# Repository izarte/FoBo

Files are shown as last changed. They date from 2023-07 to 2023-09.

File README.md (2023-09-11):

# Fobo
This project is the final degree work in robotic engineering.
Fobo is a robot whose main task is to follow you to carry your heavy weights.

It is based on a webcam with 2 degrees of freedom thanks to 2 servomotors, which, using [YOLOv8] can detect and track people in its image. The camera will follow the objective person and the robot will move based on the servomotor's position. The robot also has a depth camera used to avoid obstacles.

# Demo
Real demostration video (click on image of real FoBo):

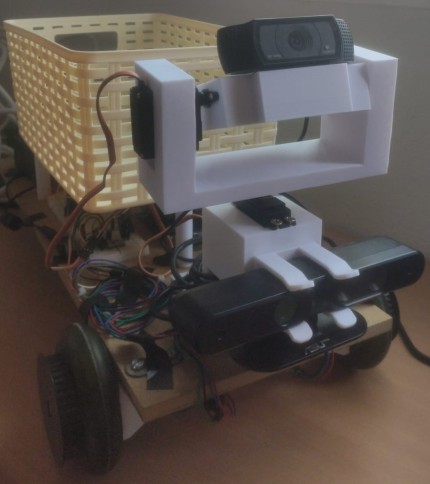
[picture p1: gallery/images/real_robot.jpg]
Demo (https://www.youtube.com/watch?v=qhu7xcjDXUQ)


# Model
All Fobo chassis have been modeled to be printed in a 3d printer. The total model can be found in [full-model]. To make the printing process easier divided model can be found in [divided-full-model].

Essential pieces to attach to a wooden board can be found in [final-real-pieces]

# Hardware
To create this robot it is necessary:
 1. NVIDIA Jetson Nano 2GB (5V 3A current)
 2. Arduino Uno
 3. Asus Xtion Pro Live
 4. Logitech C920 HD Pro Webcam
 5. 2x Stepper Motor NEMA17 (12V 2A current)
 6. 2x A4988 Stepper Driver
 7. 2x 1N4004 Diode
 8. 2x Servomotor mg945
 9. IMU MPU-6050

The following diagram shows how devices are connected

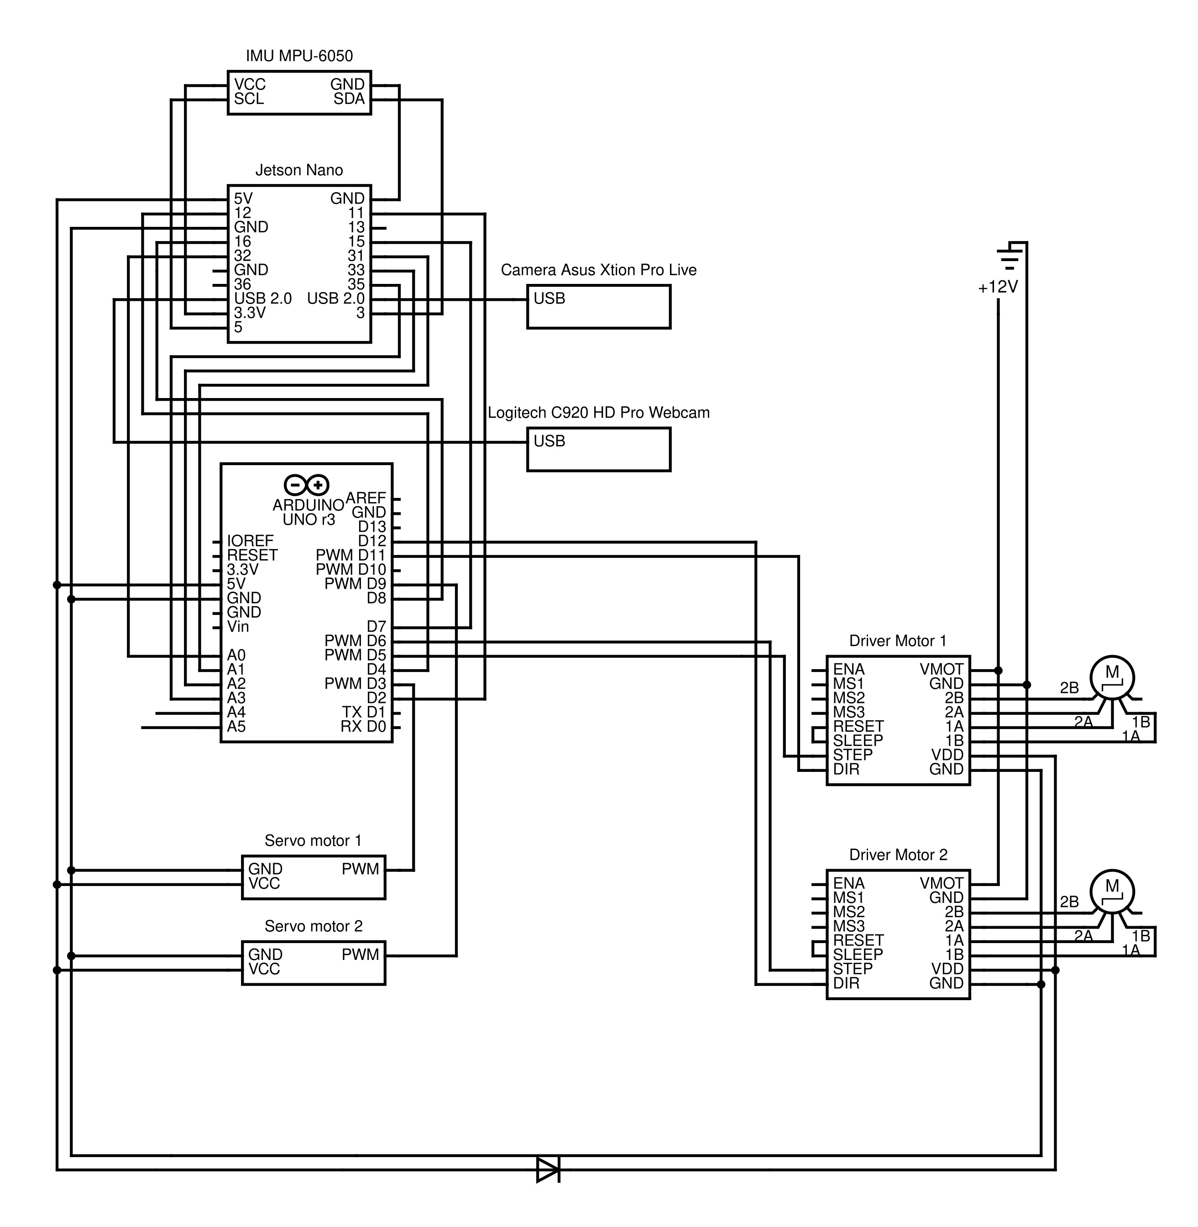
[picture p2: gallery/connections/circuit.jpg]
circuit


# Software
## Arduino

Arduino code can be found in [arduino]. This folder is a Platformio project. Code can be uploaded to Arduino via platformio.

## Jetson

### Prerequisites
1. Jetpack 4.6.2 (version L4T 32.7.1)
2. Docker (with docker-compose)

Go to [openni], a modified repository to execute in jetson nano based on [OpenNI2], and follow repository instructions.
Go to [ros2-ws] and execute the following commands to create a symbolic link to the dynamic library.
```
ln -s /usr/lib/OpenNI2
ln -s /usr/lib/libOpenNI2.so
```

After OpeNI installation, go to [jetson] folder and execute:
```
docker compose up
```

[YOLOv8]: https://github.com/ultralytics/ultralytics
[full-model]: https://github.com/izarte/FoBo/tree/main/model/full_model
[divided-full-model]: https://github.com/izarte/FoBo/tree/main/model/divided_full_model
[final-real-pieces]: https://github.com/izarte/FoBo/tree/main/model/final_real_pieces
[circuit]: https://github.com/izarte/FoBo/blob/main/gallery/connections/circuit.jpg
[arduino]: https://github.com/izarte/FoBo/tree/main/arduino
[openni]: https://github.com/izarte/FoBo/tree/main/jetson/openni/OpenNI2-TX1/OpenNI2
[OpenNI2]: https://github.com/mikeh9/OpenNI2-TX1/tree/master/OpenNI2
[ros2-ws]: https://github.com/izarte/FoBo/tree/main/jetson/ros2_ws
[jetson]: https://github.com/izarte/FoBo/tree/main/jetson

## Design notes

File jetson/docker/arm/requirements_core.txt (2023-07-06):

Jetson.GPIO==2.0.20
numpy==1.24.2
opencv-python==4.7.0.72
smbus==1.1.post2
simple-pid==2.0.0
websockets==9.1

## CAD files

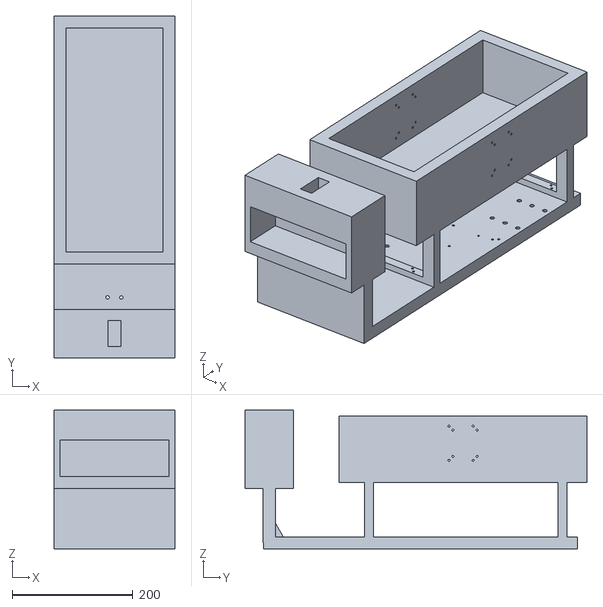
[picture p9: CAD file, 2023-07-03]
jetson/ros2_ws/src/fobo_simulation/models/own/meshes/total_model.stl
200.0 x 565.6 x 230.0

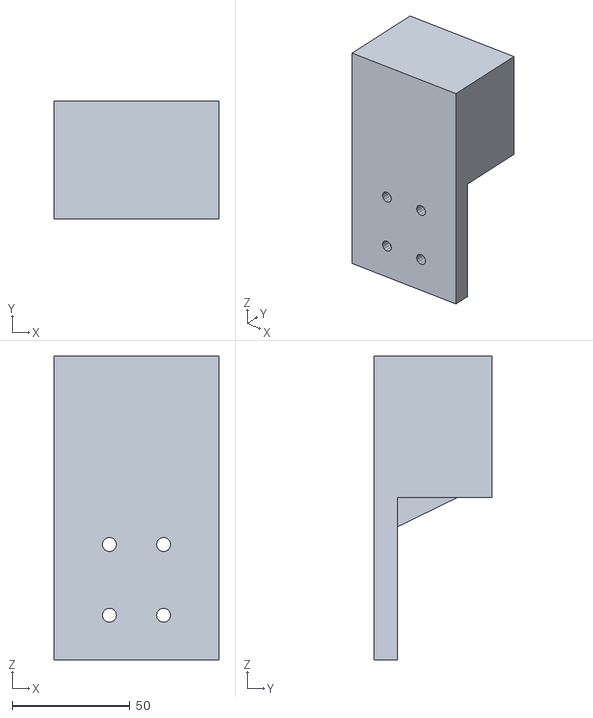
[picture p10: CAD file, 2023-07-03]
model/divided_full_model/stl/servo_piece.stl
70.0 x 50.0 x 129.0

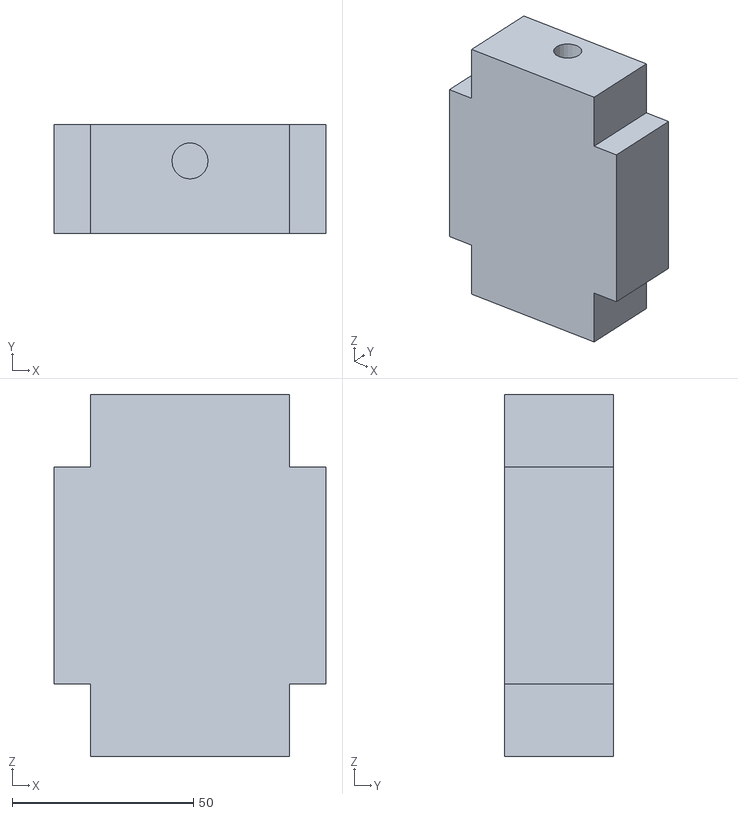
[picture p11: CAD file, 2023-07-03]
model/final_real_pieces/stl/camera_support.stl
75.0 x 30.0 x 100.0

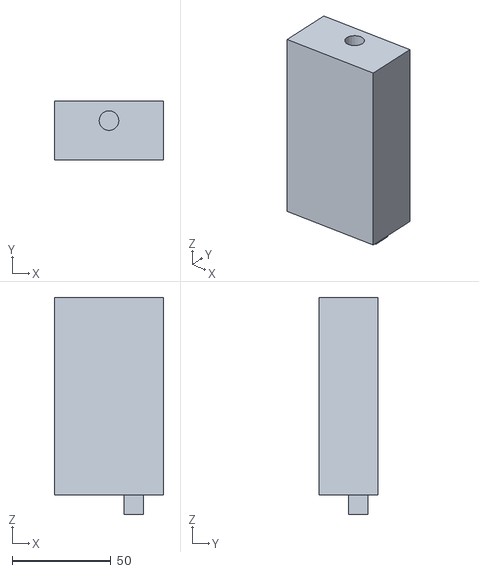
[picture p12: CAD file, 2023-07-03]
model/full_model/camera_support_2.stl
55.0 x 30.0 x 110.0

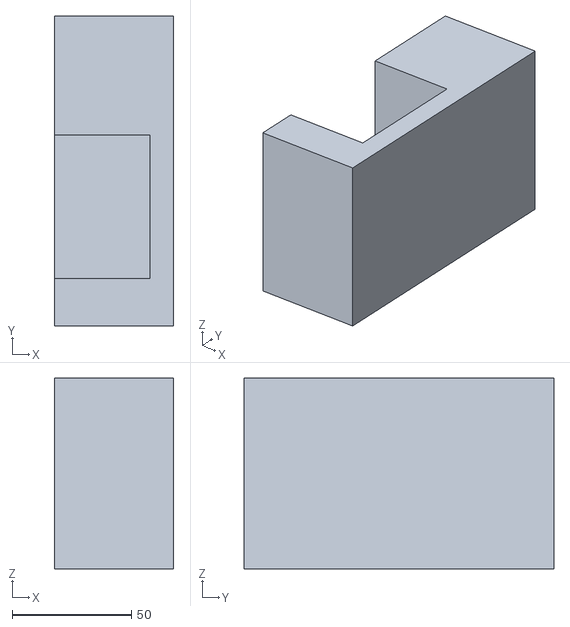
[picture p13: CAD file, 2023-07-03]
model/divided_full_model/stl/front_support_4.stl
50.0 x 130.0 x 80.0

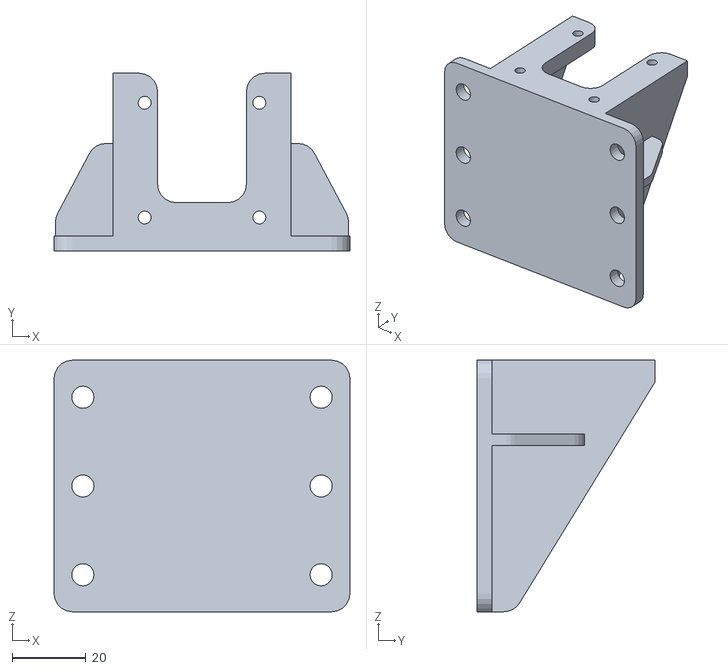
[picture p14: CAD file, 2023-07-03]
model/final_real_pieces/stl/nema17bracket_v2.stl
80.0 x 48.0 x 68.0

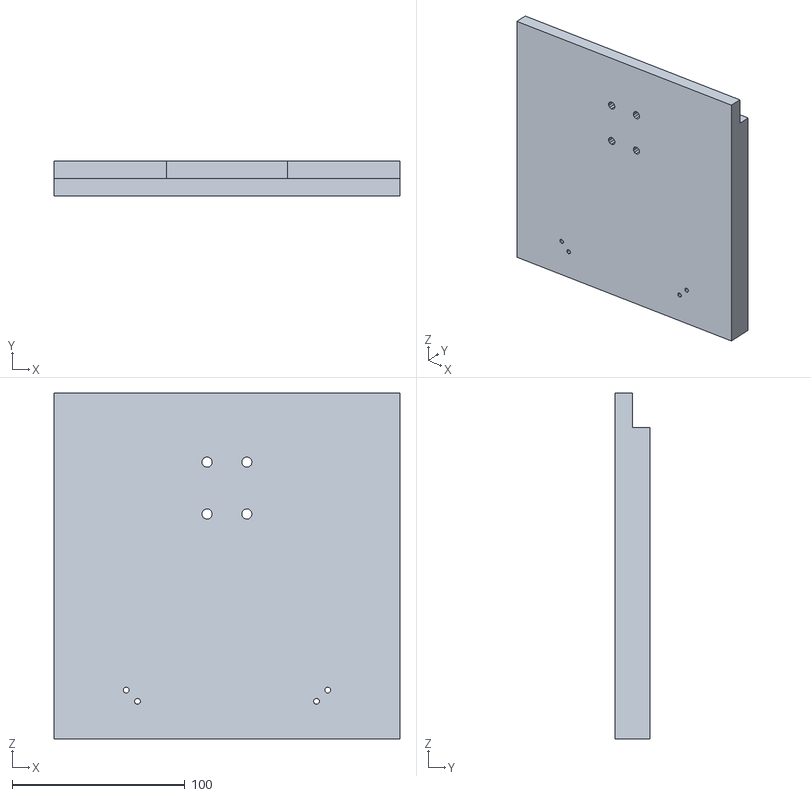
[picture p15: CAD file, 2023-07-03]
model/full_model/base_front.stl
200.0 x 20.0 x 200.0

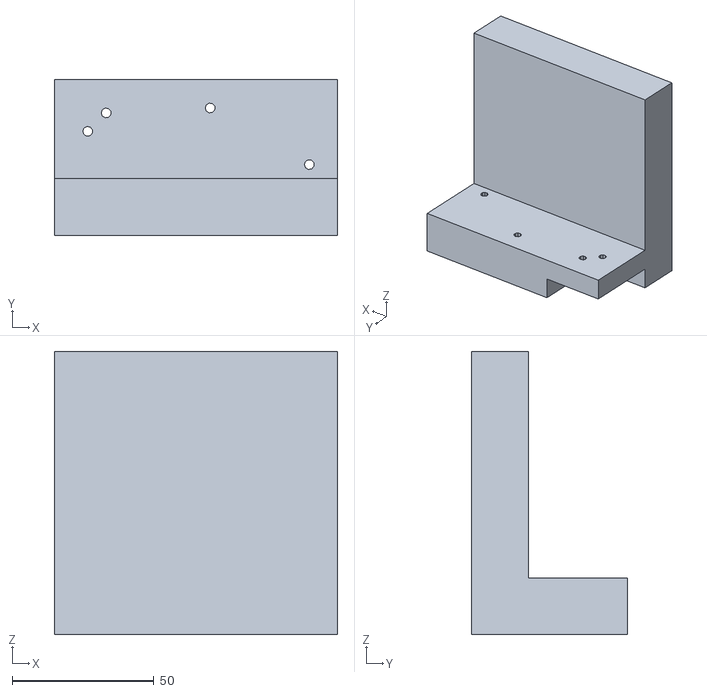
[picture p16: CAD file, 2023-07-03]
model/divided_full_model/stl/container_back_head_3.stl
100.0 x 55.0 x 100.0

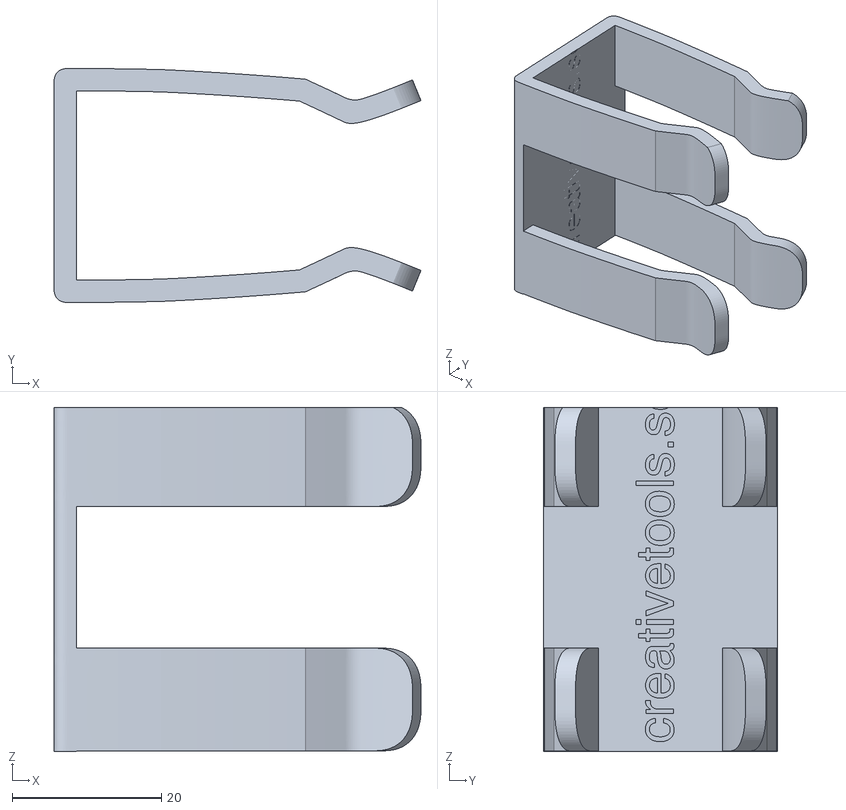
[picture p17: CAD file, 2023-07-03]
model/final_real_pieces/stl/clip_depth_camera.stl
49.3 x 31.4 x 46.2

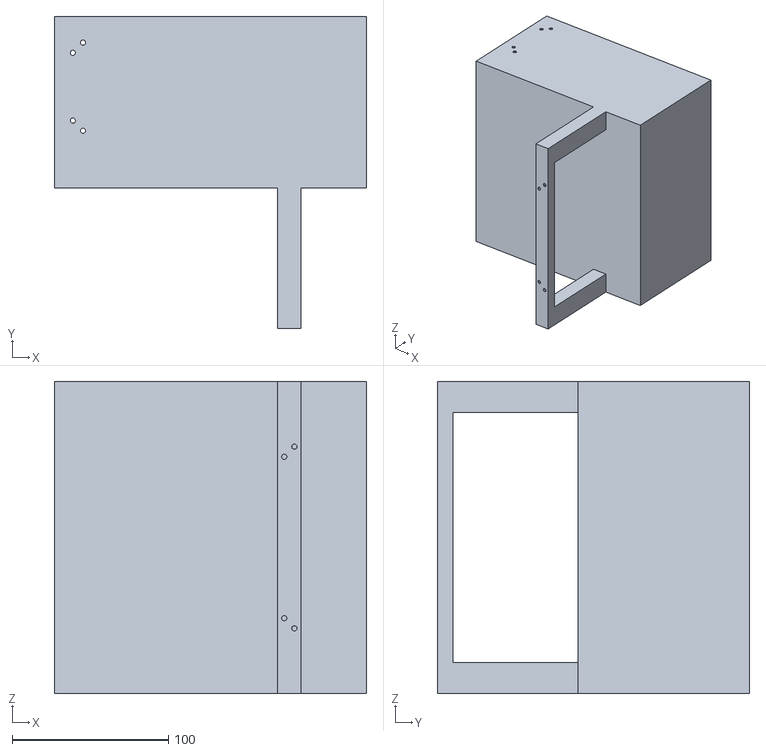
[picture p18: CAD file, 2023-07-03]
model/full_model/container_front.stl
200.0 x 200.0 x 200.0

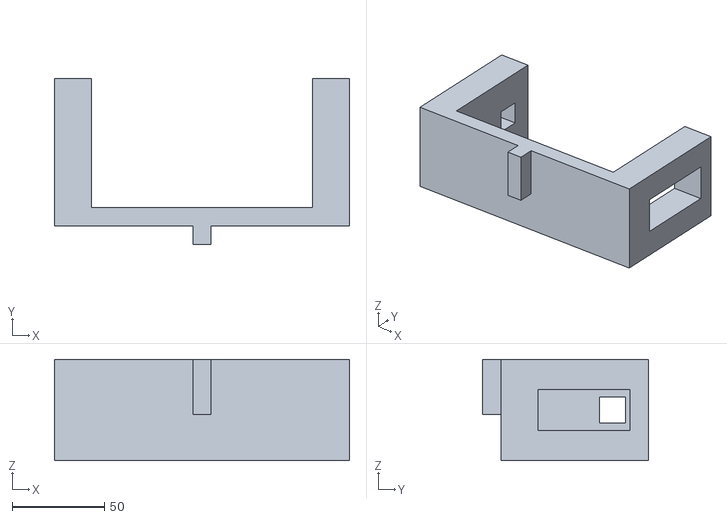
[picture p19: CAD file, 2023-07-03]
model/final_real_pieces/stl/camera_support_support.stl
160.0 x 90.0 x 55.0

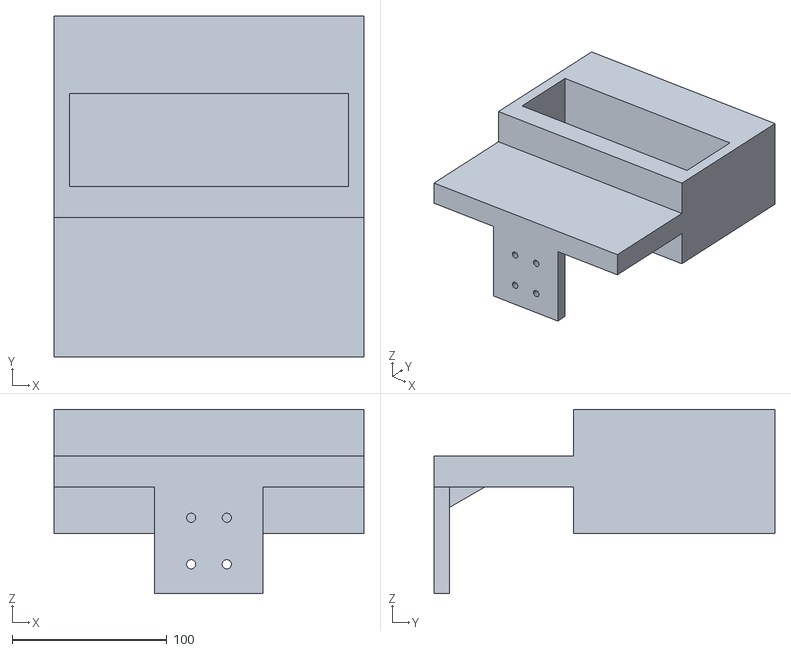
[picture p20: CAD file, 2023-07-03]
model/full_model/front_support.stl
200.0 x 220.0 x 119.0

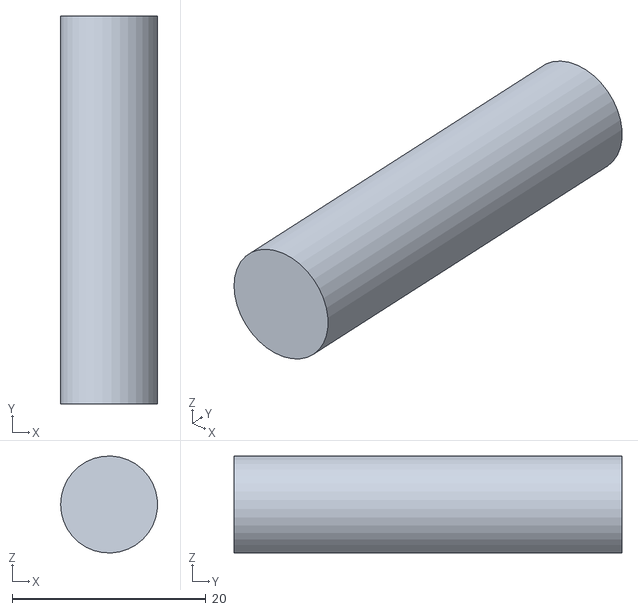
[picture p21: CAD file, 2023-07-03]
model/final_real_pieces/stl/union.stl
9.98 x 40.0 x 9.99

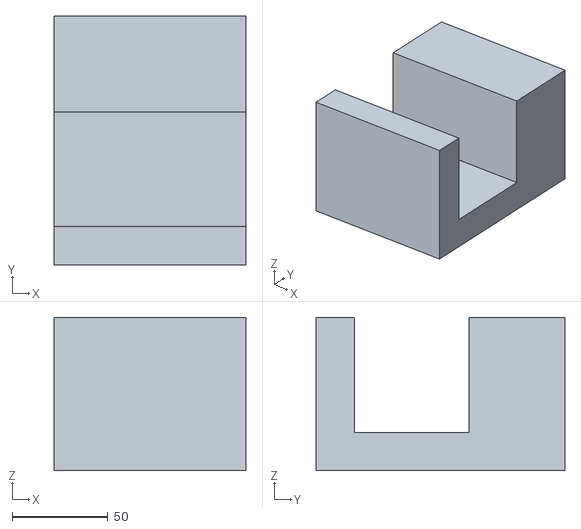
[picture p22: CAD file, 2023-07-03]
model/divided_full_model/stl/front_support_3.stl
100.0 x 130.0 x 80.0

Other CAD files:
jetson/ros2_ws/src/fobo_simulation/models/tuto/meshes/total_model.stl
model/divided_full_model/stl/front_support_2.stl
model/full_model/camera_support.stl
model/divided_full_model/4_center_union.ipt
model/divided_full_model/OldVersions/base_back.0004.ipt
model/divided_full_model/OldVersions/base_front.0004.ipt
model/divided_full_model/OldVersions/base_mid.0005.ipt
model/divided_full_model/OldVersions/camera_support.0002.ipt
model/divided_full_model/OldVersions/camera_support_2.0003.ipt
model/divided_full_model/OldVersions/container_back_foot_1.0001.ipt
model/divided_full_model/OldVersions/container_back_foot_1.0001_1.ipt
model/divided_full_model/OldVersions/container_back_head.0001.ipt
model/divided_full_model/OldVersions/container_back_head_5.0001.ipt
model/divided_full_model/OldVersions/container_back_head_7.0001.ipt
model/divided_full_model/OldVersions/container_front_foot_1.0001.ipt
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

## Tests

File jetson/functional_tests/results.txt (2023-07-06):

0:
    112
    120
    133
    123
    118
0.51:
    101
    120
    118
    126
    112
1.2:
    98
    101
    113
    115
    101

1.7:
    80
    98
    108
    110
    80
    106

2.98:
    62
    68
    56
    30
    65

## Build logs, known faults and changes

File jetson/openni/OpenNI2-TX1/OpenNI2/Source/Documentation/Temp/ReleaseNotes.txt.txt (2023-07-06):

/** @page release_notes Release Notes
OpenNI 2.3.0 Build 15
November 10 2013

Minimum Requirements:
---------------------
- Operating Systems: 
  - Windows XP with SP2 and above, Windows 7, Windows 8, on x86 (32/64 bit)
  - Ubuntu 12.04 (32/64/arm) and above
  - Android 2.3 and above
  - Mac OSX 10.7 and above
- Processors: 
  - Pentium 4, 1.4GHz and above 
  - AMD Athlon 64/FX 1GHz and above
  - Arm Cortex A8 and above
- Memory: at least 64MB available.
- 250MB free hard disk space.
- Available USB 2.0 high-speed port.
- Development Environment: 
  - Microsoft Visual Studio 2008 and 2010. The compiler can be MSVC compiler or an Intel Compiler 11 and above.
  - GCC 4.x
- Some of the sample applications require a graphics card equivalent to: ATI RADEON x1300 or NVIDIA GeForce 7300.

Prerequisets:
-------------
- Windows:
  - Microsoft Kinect SDK v1.6 (for using with Kinect devices)
    From: http://go.microsoft.com/fwlink/?LinkID=262831

- Linux:
  - LibUSB 1.0.x
    From: http://sourceforge.net/projects/libusb/files/libusb-1.0/
    Or via apt:
    sudo apt-get install libusb-1.0-0
  - LibUDEV
    sudo apt-get install libudev0
  - FreeGLUT3
    From: http://freeglut.sourceforge.net/index.php#download
    You only need the run-time version to run the OpenGL samples:
    sudo apt-get install freeglut3
    If you also want to compile the OpenGL samples, you'll need to install the development version:
    sudo apt-get install freeglut3-dev

Notes:
------
- On Android, only native support (and samples) is currently provided. Please note that as bionic (Android linker) does not
  support the rpath option, the samples cannot start as is. To solve this, do one of the following:
  - Copy OpenNI libraries (libOpenNI2.so, libPS1080.so and libOniFile.so) to /system/lib (requires root) - or -
  - run `export LD_LIBRARY_PATH=.:$LD_LIBRARY_PATH` before starting the native executeable

*/

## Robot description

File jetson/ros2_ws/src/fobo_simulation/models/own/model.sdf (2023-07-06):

<?xml version="1.0" ?>
<sdf version="1.7">
  <model name="fobo" xmlns:xacro="http://ros.org/wiki/xacro">
    <pose>0.0 0.0 0.0 0.0 0.0 0.0</pose>

    <link name="base_footprint"/>

    <joint name="base_joint" type="fixed">
      <parent>base_footprint</parent>
      <child>base_link</child>
      <pose>0.0 0.0 0.000 0 0 0</pose>
    </joint>

    <link name="base_link">
      <visual name="base_visual">
        <pose>0 0 0 0 0 0</pose>
        <geometry>
          <mesh>
            <uri>model://own/meshes/total_model.stl</uri>
            <scale>0.001 0.001 0.001</scale>
          </mesh>
        </geometry>
      </visual>



      <collision name="base_collision">
        <pose>0.1175 0.5 0.5 0 0 0</pose>
        <geometry>
          <box>
            <size>0. 0. 0.</size>
          </box>
        </geometry>
      </collision>
    </link>


    <joint name="wheel_left_joint" type="revolute">
      <parent>base_link</parent>
      <child>wheel_left_link</child>
      <pose>0.235 0.4 0.05 0 1.57 0</pose>
      <axis>
        <xyz>0 0 1</xyz>
      </axis>
    </joint>

    <link name="wheel_left_link">
      <collision name="wheel_left_collision">
        <pose>0.235 0.4 0.05 0 1.57 0</pose>
        <geometry>
          <cylinder>
            <radius>0.033</radius>
            <length>0.018</length>
          </cylinder>
        </geometry>
        <surface>
          <!-- This friction pamareter don't contain reliable data!! -->
          <friction>
            <ode>
              <mu>100000.0</mu>
              <mu2>100000.0</mu2>
              <fdir1>0 0 0</fdir1>
              <slip1>0.0</slip1>
              <slip2>0.0</slip2>
            </ode>
          </friction>
          <contact>
            <ode>
              <soft_cfm>0</soft_cfm>
              <soft_erp>0.2</soft_erp>
              <kp>1e+5</kp>
              <kd>1</kd>
              <max_vel>0.01</max_vel>
              <min_depth>0.001</min_depth>
            </ode>
          </contact>
        </surface>
      </collision>

      <visual name="wheel_left_visual">
        <pose>0.235 0.4 0.05 0 1.57 0</pose>
        <geometry>
          <cylinder>
            <radius>0.033</radius>
            <length>0.018</length>
          </cylinder>
        </geometry>
      </visual>
    </link>


    <joint name="wheel_right_joint" type="revolute">
      <parent>base_link</parent>
      <child>wheel_right_link</child>
      <pose>0.01 0.4 0.05 0 1.57 0</pose>
      <axis>
        <xyz>0 0 1</xyz>
      </axis>
    </joint>

    <link name="wheel_right_link">
      <collision name="wheel_right_collision">
        <pose>0.01 0.4 0.05 0 1.57 0</pose>
        <geometry>
          <cylinder>
            <radius>0.033</radius>
            <length>0.018</length>
          </cylinder>
        </geometry>
        <surface>
          <!-- This friction pamareter don't contain reliable data!! -->
          <friction>
            <ode>
              <mu>100000.0</mu>
              <mu2>100000.0</mu2>
              <fdir1>0 0 0</fdir1>
              <slip1>0.0</slip1>
              <slip2>0.0</slip2>
            </ode>
          </friction>
          <contact>
            <ode>
              <soft_cfm>0</soft_cfm>
              <soft_erp>0.2</soft_erp>
              <kp>1e+5</kp>
              <kd>1</kd>
              <max_vel>0.01</max_vel>
              <min_depth>0.001</min_depth>
            </ode>
          </contact>
        </surface>
      </collision>

      <visual name="wheel_right_visual">
        <pose>0.01 0.4 0.05 0 1.57 0</pose>
        <geometry>
          <cylinder>
            <radius>0.033</radius>
            <length>0.018</length>
          </cylinder>
        </geometry>
      </visual>
    </link>


    <joint name="wheel_front_joint" type="revolute">
      <parent>base_link</parent>
      <child>wheel_front_link</child>
      <pose>0.1157 0.08 0.05 0 1.57 0</pose>
      <axis>
        <xyz>0 0 1</xyz>
      </axis>
    </joint>

    <link name="wheel_front_link">
      <collision name="wheel_front_collision">
        <pose>0.1157 0.08 0.05 0 1.57 0</pose>
        <geometry>
          <cylinder>
            <radius>0.033</radius>
            <length>0.018</length>
          </cylinder>
        </geometry>
        <surface>
          <!-- This friction pamareter don't contain reliable data!! -->
          <friction>
            <ode>
              <mu>100000.0</mu>
              <mu2>100000.0</mu2>
              <fdir1>0 0 0</fdir1>
              <slip1>0.0</slip1>
              <slip2>0.0</slip2>
            </ode>
          </friction>
          <contact>
            <ode>
              <soft_cfm>0</soft_cfm>
              <soft_erp>0.2</soft_erp>
              <kp>1e+5</kp>
              <kd>1</kd>
              <max_vel>0.01</max_vel>
              <min_depth>0.001</min_depth>
            </ode>
          </contact>
        </surface>
      </collision>

      <visual name="wheel_front_visual">
        <pose>0.1157 0.08 0.05 0 1.57 0</pose>
        <geometry>
          <cylinder>
            <radius>0.033</radius>
            <length>0.018</length>
          </cylinder>
        </geometry>
      </visual>
    </link>

  </model>
</sdf>

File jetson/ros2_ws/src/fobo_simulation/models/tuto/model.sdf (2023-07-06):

<?xml version='1.0'?>
<sdf version='1.7'>
  <model name="tuto">
    <static>false</static>

    <link name="base_footprint"/>

    <joint name="base_joint" type="fixed">
      <parent>base_footprint</parent>
      <child>base_link</child>
      <pose>0.0 0.0 0.010 0 0 0</pose>
    </joint>

    <link name='base_link'>
      <pose>0 0 .1 0 0 0</pose>
    
      <collision name='collision'>
        <geometry>
          <box>
            <size>.4 .2 .1</size>
          </box>
          <pose>-0.15 0 .1 0 0 0</pose>
          <box>
            <size>0.1 .2 .1</size>
          </box>
        </geometry>
      </collision>
    
      <visual name='visual'>
        <geometry>
          <box>
            <size>.4 .2 .1</size>
          </box>
        </geometry>
      </visual>

      <visual name='front_up'>
      <pose>-0.15 0 .1 0 0 0</pose>
        <geometry>
          <box>
            <size>0.1 .2 .1</size>
          </box>
        </geometry>
      </visual>

      <collision name='caster_collision'>
        <pose>-0.15 0 -0.05 0 0 0</pose>
        <geometry>
            <sphere>
            <radius>.05</radius>
          </sphere>
        </geometry>
      
        <surface>
          <friction>
            <ode>
              <mu>0</mu>
              <mu2>0</mu2>
              <slip1>1.0</slip1>
              <slip2>1.0</slip2>
            </ode>
          </friction>
        </surface>
      </collision>
      
      <visual name='caster_visual'>
        <pose>-0.15 0 -0.05 0 0 0</pose>
        <geometry>
          <sphere>
            <radius>.05</radius>
          </sphere>
        </geometry>
      </visual>
    </link>


    <link name="wheel_left_link">
      <pose>0.1 0.13 0.1 0 1.5707 1.5707</pose>
      <collision name="collision">
        <geometry>
          <cylinder>
            <radius>.1</radius>
            <length>.05</length>
          </cylinder>
        </geometry>
      </collision>
      <visual name="visual">
        <geometry>
          <cylinder>
            <radius>.1</radius>
            <length>.05</length>
          </cylinder>
        </geometry>
      </visual>
    </link>

    <link name="wheel_right_link">
      <pose>0.1 -0.13 0.1 0 1.5707 1.5707</pose>
      <collision name="collision">
        <geometry>
          <cylinder>
            <radius>.1</radius>
            <length>.05</length>
          </cylinder>
        </geometry>
      </collision>
      <visual name="visual">
        <geometry>
          <cylinder>
            <radius>.1</radius>
            <length>.05</length>
          </cylinder>
        </geometry>
      </visual>
    </link>

    <joint type="revolute" name="wheel_left_joint">
      <pose>0 0 -0.03 0 0 0</pose>
      <parent>base_link</parent>
      <child>wheel_left_link</child>
      <axis>
        <xyz>0 0 -1</xyz>
      </axis>
    </joint>
    
    <joint type="revolute" name="wheel_right_joint">
      <pose>0 0 0.03 0 0 0</pose>
      <parent>base_link</parent>
      <child>wheel_right_link</child>
      <axis>
        <xyz>0 0 -1</xyz>
      </axis>
    </joint>


    <link name="camera_link">
      <pose>-0.15 0 .3 0 0 0</pose>
      <collision name="collision">
        <geometry>
          <box>
            <size>0.05 .1 .05</size>
          </box>
        </geometry>
      </collision>
      <visual name="visual">
        <geometry>
          <box>
            <size>0.05 .1 .05</size>
          </box>
        </geometry>
      </visual>

      <sensor name="depth_camera" type="camera">
        <always_on>true</always_on>
        <visualize>false</visualize>
        <update_rate>5</update_rate>
        <camera name="camera">
          <horizontal_fov>1.02974</horizontal_fov>
          <image>
            <width>640</width>
            <height>480</height>
            <format>R8G8B8</format>
          </image>
          <clip>
            <near>0.02</near>
            <far>10</far>
          </clip>
          <noise>
            <type>gaussian</type>
            <!-- Noise is sampled independently per pixel on each frame.
                That pixel's noise value is added to each of its color
                  channels, which at that point lie in the range [0,1]. -->
            <mean>0.0</mean>
            <stddev>0.007</stddev>
          </noise>
        </camera>
        <plugin name="depth_camera_controller" filename="libgazebo_ros_camera.so">
          <camera_name>camera_link</camera_name>
          <frame_name>camera_link_frame</frame_name>
          <hack_baseline>0</hack_baseline>
          <min_depth>0.001</min_depth>
        </plugin>
      </sensor>
    </link>

    <joint type="revolute" name="camera_base_joint">
      <pose>-0.15 0 .3 0 0 0</pose>
      <parent>base_link</parent>
      <child>camera_link</child>
      <axis>
        <xyz>1 0 0</xyz>
      </axis>
    </joint>

    <transmission name="camera_base_tran">
      <type>transmission_interface/SimpleTransmission</type>
      <joint name="camera_base_joint">
        <hardwareInterface>EffortJointInterface</hardwareInterface>
      </joint>
      <actuator name="camera_base">
        <mechanicalReduction>1.0</mechanicalReduction>
        <hardwareInterface>EffortJointInterface</hardwareInterface>
      </actuator>
    </transmission>

    <gazebo>
      <plugin name="gazebo_ros_control" filename="libgazebo_ros_control.so">
        <robotNamespace>/fobo</robotNamespace>
      </plugin>
    </gazebo>

    <!-- Controls the differential drive robot -->
    <plugin name='diff_drive' filename='libgazebo_ros_diff_drive.so'>
      <ros>
        <namespace>/fobo</namespace>
        <remapping>cmd_vel:=cmd_vel</remapping>
        <remapping>odom:=odom</remapping>
      </ros>

      <!-- wheels -->
      <left_joint>wheel_left_joint</left_joint>
      <right_joint>wheel_right_joint</right_joint>

      <!-- kinematics -->
      <wheel_separation>0.26</wheel_separation>
      <wheel_diameter>0.2</wheel_diameter>

      <!-- limits -->
      <max_wheel_torque>20</max_wheel_torque>
      <max_wheel_acceleration>1.0</max_wheel_acceleration>

      <!-- output -->
      <publish_odom>true</publish_odom>
      <publish_odom_tf>true</publish_odom_tf>
      <publish_wheel_tf>true</publish_wheel_tf>

      <odometry_frame>odom</odometry_frame>
      <robot_base_frame>chassis</robot_base_frame>
    </plugin>
  </model>
</sdf>

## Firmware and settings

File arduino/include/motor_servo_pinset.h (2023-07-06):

#ifndef MOTOR_SERVO_PINSET_H

#define MOTOR_SERVO_PINSET_H

#include <Servo.h>
#include <Arduino.h>

// init.cpp
void init_servos();
void init_motors();

// servo.cpp
void servo_control();
void modify_angle(int *angle, int delta);
void blinkLed(int t);

// Stepper
void motors_control();

const int LED = 13;

// Motor 1 constant pins
const int MOTOR_1_STEP = 5;
const int MOTOR_1_DIRECTION = 11;
const int MOTOR_1_SPEED_INPUT = A0;             // Jetson 33
const int MOTOR_1_DIRECTION_INPUT = A1;         // Jetson 31 (200)

// Motor 2 constant pins
const int MOTOR_2_STEP = 6;
const int MOTOR_2_DIRECTION = 12;
const int MOTOR_2_SPEED_INPUT = A2;             // Jetson 32
const int MOTOR_2_DIRECTION_INPUT = A3;         // Jetson 35 (76)

// Servo 1 pimap
const int PIN_SERVO_1 = 3;
const int SERVO_1_INCR = 2;                    // Jetson 11 (50)
const int SERVO_1_DIR = 4;                     // Jetson 12 (79)
// Servo 2 pinmap
const int PIN_SERVO_2 = 9;
const int SERVO_2_INCR = 7;                    // Jetson 15 (194)
const int SERVO_2_DIR = 8;                     // Jetson 16 (232)

const int delta_x = 3;
const int delta_y = 2;


#endif

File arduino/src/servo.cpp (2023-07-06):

#include "motor_servo_pinset.h"

extern Servo servo_1;
extern Servo servo_2;
extern int angle_servo_1;
extern int angle_servo_2;

int last_read_incr_1 = 1;
int last_read_incr_2 = 1;

int read_incr_1 = 0;
int read_dir_1 = 1;
int read_incr_2 = 0;
int read_dir_2 = 1;

int blink_time = millis();


void servo_control()
{
    read_incr_1 = !digitalRead(SERVO_1_INCR);
    read_dir_1 = !digitalRead(SERVO_1_DIR);
    read_incr_2 = !digitalRead(SERVO_2_INCR);
    read_dir_2 = !digitalRead(SERVO_2_DIR);

    if (read_incr_1 && !last_read_incr_1)
    {
        blinkLed(millis());
        if (read_dir_1)
            modify_angle(&angle_servo_1, -delta_x);
        else
            modify_angle(&angle_servo_1, delta_x);
        servo_1.write(angle_servo_1);
        Serial.println(angle_servo_1);
    }

    if (read_incr_2 && !last_read_incr_2)
    {
        blinkLed(millis());
        if (read_dir_2)
            modify_angle(&angle_servo_2, -delta_y);
        else
            modify_angle(&angle_servo_2, delta_y);
        servo_2.write(angle_servo_2);
        Serial.println(angle_servo_2);
    }

    last_read_incr_1 = read_incr_1;
    last_read_incr_2 = read_incr_2;
    blinkLed(0);
}


void modify_angle(int *angle, int delta)
{
    *angle += delta;
    if (*angle > 180)
    {
        *angle = 180;
        return;
    }
    if (*angle < 0)
    {
        *angle = 0;
        return;
    }
    return;
}


void blinkLed(int t)
{
    if ((!t && millis() > blink_time + 1000) || !blink_time)
    {
        blink_time = 0;
        digitalWrite(LED, LOW);
    }
    if (t)
    {
        digitalWrite(LED, HIGH);
        blink_time = t;
    }
}

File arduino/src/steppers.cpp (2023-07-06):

#include "motor_servo_pinset.h"

// Variables initialaztion for motor 1
int speed_input_1 = 0;
int step_state_1 = 0;
unsigned long prev_time_1 = micros();
unsigned long step_delay_1 = 600;

// Variables initialaztion for motor 2
int speed_input_2 = 0;
int step_state_2 = 0;
unsigned long prev_time_2 = micros();
unsigned long step_delay_2 = 600;

unsigned long actual_time = micros();


void motors_control()
{
    // Read PWM signal input
    speed_input_1 = analogRead(MOTOR_1_SPEED_INPUT);
    speed_input_2 = analogRead(MOTOR_2_SPEED_INPUT);

    // Set direction motors, inversed due to pullup
    digitalWrite(MOTOR_1_DIRECTION, digitalRead(MOTOR_1_DIRECTION_INPUT));
    digitalWrite(MOTOR_2_DIRECTION, digitalRead(MOTOR_2_DIRECTION_INPUT));

    actual_time = micros();
    
    // Motor 1 control
    if (speed_input_1 > 50 && actual_time - prev_time_1 > step_delay_1)
    {
        prev_time_1 = actual_time;
        step_delay_1 = map(speed_input_1, 10, 1023, 1200, 400);
        digitalWrite(MOTOR_1_STEP, step_state_1);
        step_state_1 = !step_state_1;
    }

    // Motor 2 control
    if (speed_input_2 > 50 && actual_time - prev_time_2 > step_delay_2)
    {
        prev_time_2 = actual_time;
        step_delay_2 = map(speed_input_2, 10, 1023, 1200, 400);
        digitalWrite(MOTOR_2_STEP, step_state_2);
        step_state_2 = !step_state_2;
    }
}

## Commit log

2022-06-15 add first model
    [main_base.0005.ipt, main_base.ipt, motor_fastening.0002.ipt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]
2022-10-09 add combined pieces
    [Ensamblaje1.0001.iam, Ensamblaje1.iam, base.0001.ipt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]
2022-10-28 complete model, start partitioning
    [Ensamblaje1.0001.iam, Ensamblaje1.0003.iam, Ensamblaje1.iam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]
2022-10-28 fit base back and mid back
    [base_back.0003.ipt, base_back.0006.ipt, base_back.ipt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]
2022-10-30 create sliced container
    [base_back.0006.ipt, base_back.0007.ipt, base_back.ipt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]
2022-10-31 create front support piece
    [base.0009.ipt, base.0010.ipt, base.ipt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]
2022-11-29 Add all models
    [arduino.ipt, arduino_case.stl, base_back.0007.ipt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]
2022-11-29 Remove big design, adjust to 20x20x23
    [Ensamblaje1.iam, base_back.ipt, base_back.stl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]
2023-02-10 Add initial files with pinmaps, servo control and pwm readen
2023-02-12 Add motor control with pwm signal
2023-02-13 Add Arduino code to control all motors
2023-02-13 Add divided pieces and stl models
    [4_center_union.ipt, base_back.0004.ipt, base_back.ipt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]
2023-02-13 Add circuit desing
2023-03-10 Add jetson control
    [common_properties.urdf, fobo.urdf, lds.stl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]
2023-03-12 Clean repo and add first steps in creating model simulation
    [fobo.urdf, model.sdf, own.urdf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]
2023-03-12 Rotated model
    [rotated_total_model.iam, total_model.0008.iam, total_model.0009.iam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]
2023-03-17 Add model design simulation
    [model.sdf, total_model.stl]
2023-03-20 Remove install package
    [common_properties.urdf, lds.stl, left_tire.stl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]
2023-03-23 Change stepper communication arduino
2023-03-23 Chane servo communication jetson
2023-03-24 Add dockerfile for arm
2023-03-24 Add camera detection node
2023-03-25 Add move control based on servo angle
2023-04-09 Add ros2 to docker cuda, change angle delta in servos
2023-04-25 Reduced front support base
    [camera_support.stl, camera_support_2_1.stl, camera_support_2_2.stl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]
2023-05-13 Add yolov8 Dockerfile with contanirez application for detect, track and publish in ros
2023-05-17 Reduce to 2 delta y motor
2023-05-18 Add dockerfile for yolo, change y motor delta to 3
2023-05-25 Add noise filter to servos
    [servo.cpp]
2023-05-27 Add servo piece
    [servo_piece.0001.ipt, servo_piece.ipt, servo_piece.stl]
2023-05-27 Add depth_camera_support
    [camera_support.0001.ipt, camera_support.ipt, camera_support.stl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]
2023-05-30 Restore servo movemente on high edge
2023-06-03 Migrate arduino code to palatformio and add gyroscope
2023-06-03 Remove last arduino project, complete arduino migration in platformio
2023-06-15 Add functional test for imu
2023-06-18 Add read imu and refactored messages
2023-06-18 Add dockerfiles for arm and new yolo
2023-06-18 Add arduino and jetson
2023-07-03 Organize models
    [4_center_union.ipt, Ensamblaje1.0003.iam, arduino.ipt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]
